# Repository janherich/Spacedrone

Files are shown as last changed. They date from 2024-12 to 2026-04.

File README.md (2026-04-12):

# Spacedrone
High-performance open-source scalable drone project
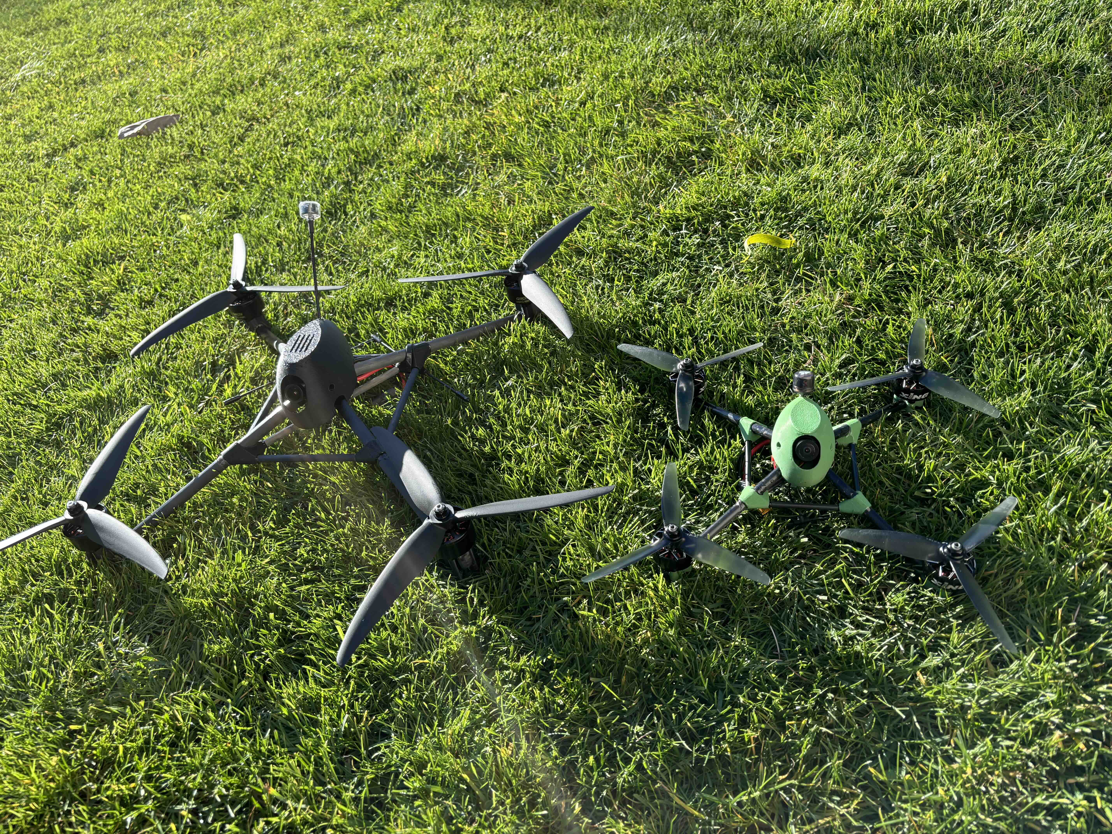
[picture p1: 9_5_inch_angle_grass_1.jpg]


<video controls width="100%" preload="metadata">
  <source src="/5_inch_pyramid_drone/video/spirited_flying.mp4" type="video/mp4">
  Your browser does not support the video tag.
</video>

# About Spacedrone
## Rationale

Spacedrone aims to approach quadrocopter design from a very different angle compared to existing projects.
It utilises efficient spaceframe structures and aerodynamic principles to create a very efficient quadcopter
design, with lowest-in-class weight and above-average frame stiffness ([7" stiffness comparison](7_inch_pyramid_drone/STIFFNESS_COMPARISON.md)) and aerodynamics.

Furthermore, it is fully parametric and scalable, covering a wide range of sizes—from small sub-250g 4–5" builds to
heavy lifters with 3115 and bigger motors.

## 5-inch racer
* [Project folder with build instructions and 3D print files](/5_inch_pyramid_drone)
* ~38g complete frame weight with aerodynamic canopy
* Recommended for milder ~1800kv 6s motors
* ~250g average build weight with powerful 2207/2306 motors, 230g possible with very light motors motors and titanium hardware
* Perfect balance with bottom mounted battery, CG in the propeller plane
* Integral cable routing in hollow 7mm round arms, no braces or additional obstructions in propeller airflow
* Aerodynamic canopy with quick attach system housing camera, vtx and RX
* Almost completely clean camera view with just small parts of motors in the bottom corners of the viewport, despite balanced true-X config
* Stiff frame capable of running aggressive PID tunes without hot-motors/vibration problems

## 5-inch HD racer
* [Project folder with build instructions and 3D print files](/5_inch_hd_pyramid_drone)
* ~48g complete frame weight with aerodynamic canopy
* Recommended for the most powerful ~2100kv 6s motors
* ~270g average build weight with powerful 2207/2306 motors, 260g possible with titanium hardware
* Perfect balance with bottom mounted battery, CG in the propeller plane
* Integral cable routing in hollow 8mm round arms, no braces or additional obstructions in propeller airflow
* Aerodynamic canopy with quick attach system housing camera, vtx and RX
* Almost completely clean camera view with just small parts of motors in the bottom corners of the viewport, despite balanced true-X config
* Stiff frame capable of running aggressive PID tunes without hot-motors/vibration problems
* Easily achieves ([240km/h+ top speed](5_inch_hd_pyramid_drone/img/flight_stats.png)) even with standard mid-pitch 5.1" tri-blades

## 7-inch long-range cruiser
* [Project folder with build instructions and 3D print files](/7_inch_pyramid_drone)
* ~60g complete frame weight with aerodynamic canopy
* ~300g average build weight with efficient 2506/2604 motors, 280g possible with smaller, lower kv 2207 or similar sized motors
* Perfect balance with bottom mounted battery, CG in the propeller plane
* Integral cable routing in hollow 8mm round arms, no braces or additional obstructions in propeller airflow
* Aerodynamic canopy with quick attach system housing camera, vtx and RX
* Very clean camera view with just small parts of propellers/motors in bottom corners of the viewport, despite balanced true-X config
* Stiff frame capable of running aggressive PID tunes without hot-motors/vibration problems ([stiffness comparison vs standard 7" frame](7_inch_pyramid_drone/STIFFNESS_COMPARISON.md))

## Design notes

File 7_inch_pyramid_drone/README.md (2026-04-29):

# Build guide

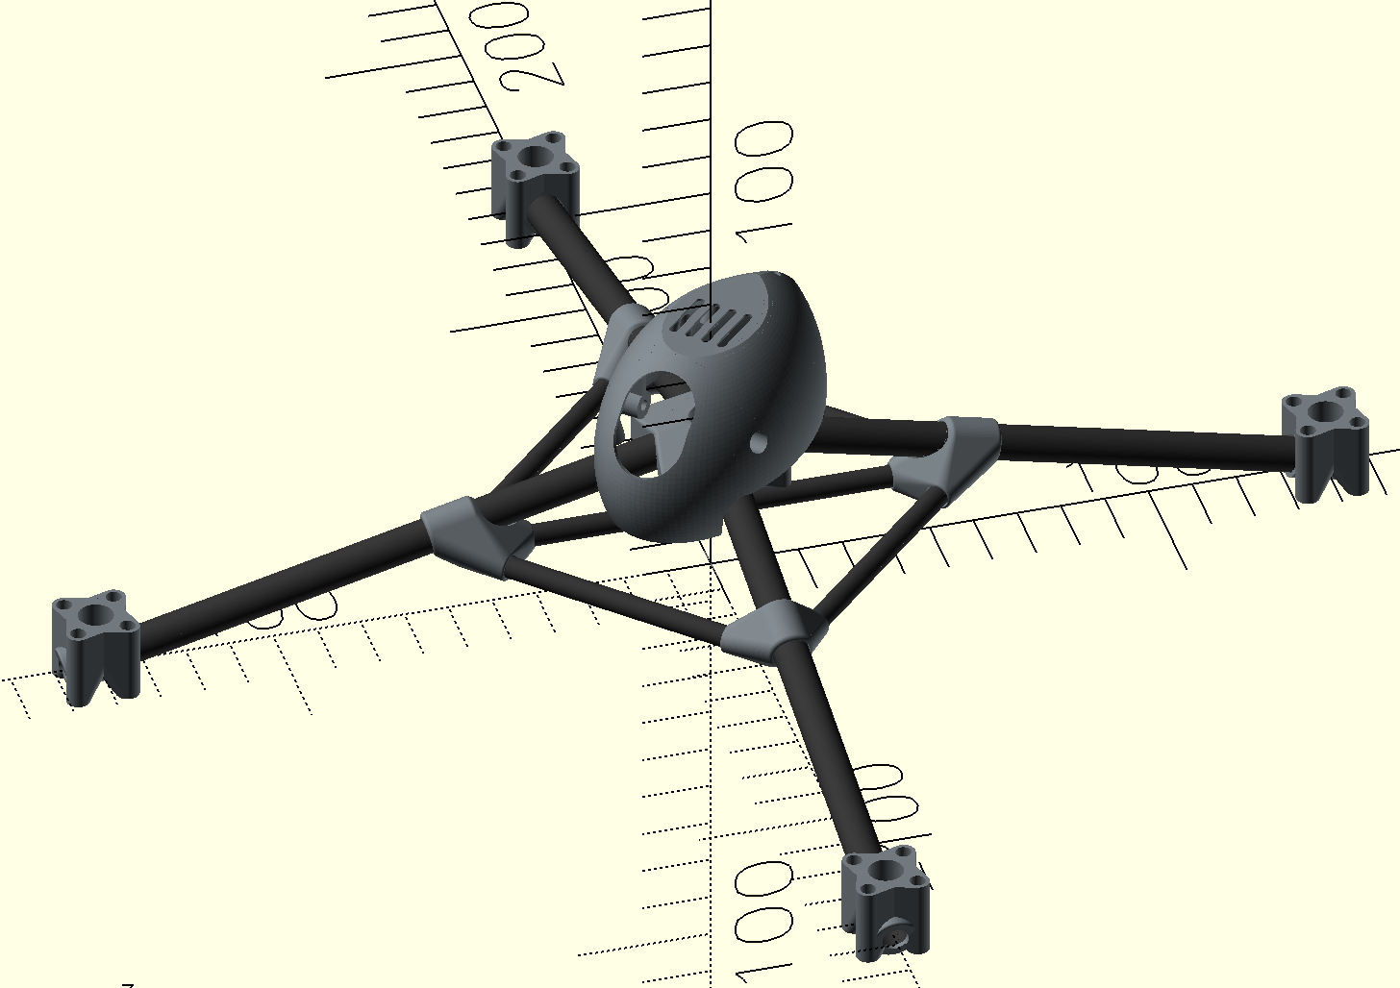
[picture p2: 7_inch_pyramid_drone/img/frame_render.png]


See [Stiffness comparison](STIFFNESS_COMPARISON.md) for test results vs a standard 7" frame.

## List of parts

### 3D Printed parts
* 1x `canopy.stl` (or `canopy_long_camera_bolts.stl`)
* 1x `central_top_node.stl`
* 2x `arm_corner_0.stl`
* 2x `arm_corner_1.stl`
* 4x `motor_mount.stl`
* 4x `canopy_snap_on_anchor.stl`
* 2x `battery_rail.stl`

### Carbon tubing
* 1x 106mm long 5x3 tube (diagonal brace)
* 4x 78.5mm long 5x3 tube (perimeter brace)
* 4x 147.6mm long 8x6 tube (arm tube)

### Metal fasteners
* 16x M3x20mm motor bolts
* 4x M2x12mm flight controller mount bolts

### Tools and consumables
* Structural epoxy, 30min set-time is ideal, or alternatively MMA adhesive
* Small cut-off saw for cutting carbon tubing (hacksaw with very fine toothed blade works as well)
* Small strip of sandpaper or flat file to scratch tube mating surfaces

### Drone parts
* 1x AIO board (Speedybee F405 AIO is a good choice)
* 4x 16mm mount pattern motors, 2506 or 2604 size is a good choice
* 4x 7-7.5" Props (7.5" is the max diameter supported by the frame)
* Small VTX with 20x20 mount pattern
* VTX Antenna with right angle MMCX connector
* Micro sized cam (19mm camera spacing)
* RX (small size; HGLRC ELRS 2.4G is a good choice)

## Assembly instructions

### Assembling the frame

Print all parts with suitable material, PETG, PC or PA12CF15 are all good choices.
PLA is brittle and its impact resistance is poor, but it's also very stiff - frame will be
the stiffest, but impact resistance will suffer.

Standard print settings with 2-3walls, 20% infill and 4 top/bottom layers are good, keep cooling
at minimum (max 40%) to achieve good layer adhesion, no supports are necessary.

Cut CFRP tubing to necessary length using cut-off saw with carbide/diamond cutting disc (fastest and cleanest method),
or manual hacksaw with fine toothed blade. 
Try to cut the tubes as precisely as possible, it's better to cut the tubes a little bit longer and carefully shorten
them to the desired length with a flat diamond file.

Once tubes are cut, you need to thoroughly scratch the mating surfaces with a flat file for a good epoxy bond.
Scratching is not necessary with raw carbon pultruded tubes, like [DPP pultruded tubes](https://www.dpp-pultrusion.com/en-NL),
it's enough to clean and degrease them with IPA.

Next step is glueing the frame together. I recommend good structural epoxy with 30min set-time - while MMA adhesives
like [MD Megabond 3000](https://www.marstondomsel.de/index.php/en/product/md-megabond-3030) provide the best strength and
impact resistance, their set-time is usually quite short and their fumes are nasty.

It's easiest to divide glueing into 3 steps:
1. First, glue motor mounts on arm tube ends—test with a dry fit before; the motor mount needs to fit on the tube without excessive force.
Mix epoxy and apply it to the scratched/sanded end of the motor arm tube, then insert the tube into motor mount.
Make sure the tube is inserted all the way and rotate it couple of times to distribute epoxy evenly.
Be careful not to clog the end of the tube with epoxy, as it needs to remain clear for motor cable routing - remove the excess epoxy with piece of paper/towel in case some got into the tube.

2. As a second step, assemble the central support perimeter with diagonal tube.
Do a dry fit test before, making sure that tubes can be inserted into corner nodes easily and perimeter is square and lying flat on workbench.
Next, mix epoxy and put it inside each support tube hole/cavity (use a wooden stick for that).
Take 2 bigger corner nodes, mount them on diagonal tube and lay it on the workbench.
Take one of the smaller corner pieces and put 2 perimeter tubes into holes/sockets, repeat the same process for the last corner piece.
In the final assembly step, pull the 2 bigger corners with the diagonal tube a little bit apart and join them with the rest of the pieces.
Once every tube is inside corner piece socket, press all corners together with your fingers and lay it flat on workbench.
You will need to wait till the epoxy cures for the last step.

3. Next, prepare the arm tubes with already mounted motor mounts (step 1) - make sure the through holes for 12mm long motor bolts are clear and bolts
can be inserted without problems. 
Once all bolt channels are ready, mount the bolts into motor mount, fixing them with nuts on the other side, so they don't fall out.
Alternatively, you can already mount motors, making sure the motor wires are facing outside the frame center, exactly opposite how would you normally mount them on a classic quad frame.

Test fit by inserting arm tubes (already with attached motor mounts) through the corners and joining them together with the central top node.
The best way to do it is to first put 2 arm tubes through the smaller corner nodes (the ones joined by just 2 perimeter tubes, without the diagonal tube), and join them with the central node.
You can then use the cable hole in the central node + diagonal tube below it to visually center the arm tubes - put the remaining 2 arm tubes through the bigger perimeter corners afterwards and join them in the central node as well.
They should fit easily without excessive force and you should be able to easily rotate the arm tubes when the whole frame is assembled.
Put the frame on flat workbench, arm ends with motor mounts should be level when they rest on motor bolt heads and frame shouldn't be twisted, all 4 arm ends should be touching the bench.

Next, pull the arm tubes a little bit (1–2 cm) apart and remove the central node.
Mix epoxy and spread it on the arm tube just outside of the perimeter corner, cover a ~10mm band on the tube with epoxy, don't put too much there, just a thin layer.
Lift the frame (hold it by the perimeter tubes; avoid touching epoxied or to-be-epoxied parts) and slowly push the arm tube you just epoxied ~2 cm inside through the corner piece while rotating it at the same time, then pull it back.
The aim is to evenly spread the epoxy inside the corner piece, repeat for each arm-tube/corner.
As a last step, spread epoxy on arm-tube ends (to be joined by the central top node), be careful to just spread it on the outside of the tube. Attach the central node, using the same sequence of steps as described
above in the (dry) fit test section, rotate each arm tube 2-3 times to spread the epoxy evenly, make sure that each tube is inserted fully to the end-stop in the central node and put the frame on flat workbench.
Make sure everything is aligned and level and wait for the epoxy to fully cure.

### Assembling the canopy housing

Put a bit of glue (epoxy or CA) on protruding sticks of canopy anchors and insert them into canopy anchor sockets.
Rotate the anchors in correct fashion - you can snap the canopy on frame and the anchors will align, wait for glue to set before removing the canopy.

### Mounting frame components

1, Start by mounting motors, bolt each motor to mount on arm end in such a way that wires face outside of the frame center. 
Do not shorten the motor wires, you need at least 20cm long wires when routed internally.
Guide the wires through the hollow arm tube till you can see the wire ends in central node hole, then "fish" them out from the top hole with tweezers or a small piece of bent wire. 
Once you have all 3 motor wires out tie them together with a small strip of tape, so you don't mix up wires from separate motors later, 
when soldering them to ESC pads. 
You can even color mark wire before routing them through the tube, so you can solder them in the right order and you don't have to mess with motor direction in firmware later.

An alternative and slightly easier way is to mount motors in a standard way, with wires facing inwards, simply taped to the tube top side.
I think it's a shame to not take advantage of the unique internal routing capability of this frame and resulting better aesthetics & aerodynamics, but it's up to you.

2. Prepare AIO board by soldering battery leads, capacitor and CAM/VTX/RX connections.

3. Mount AIO board by placing it between top node and diagonal bracing tube and screwing bolts (M2x12mm) directly to holes in the central node.
Board needs to be flipped upside down, so that USB connector and solder pads are accessible.

After board is fixed, solder the motor wires to ESC pads.

4. Fix the camera inside canopy with side bolts, connect it to camera wire from AIO.
Guide the antenna with MMCX connector through the antenna tube and connect it to VTX.
Mount the VTX with 2 M2 bolts into the VTX screw-in sockets; fix the RX board with double-sided tape inside the canopy,
good place is front below the camera window for front mounted rx antenna/s, or rear of the canopy for rear rx antenna location.
Now you can tuck-in all connector wires inside canopy and snap canopy in place.

5. Secure RX antenna with zip tie or electrical tape on front or rear arm (8mm).
Secure battery leads from AIO on rear perimeter tube (5mm) with zip tie as well.

### Mounting battery

Battery is mounted below the frame between 2 snap-on battery rails.
Adjust their width to fit the chosen battery; you can also tape non-slip silicone strips on the rails for better grip.
Battery securing strip is threaded just below the diagonal tube.

For Betaflight setup and flight video, see **[Configuration](CONFIGURATION.md)**.

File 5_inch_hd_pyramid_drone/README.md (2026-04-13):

# Build guide

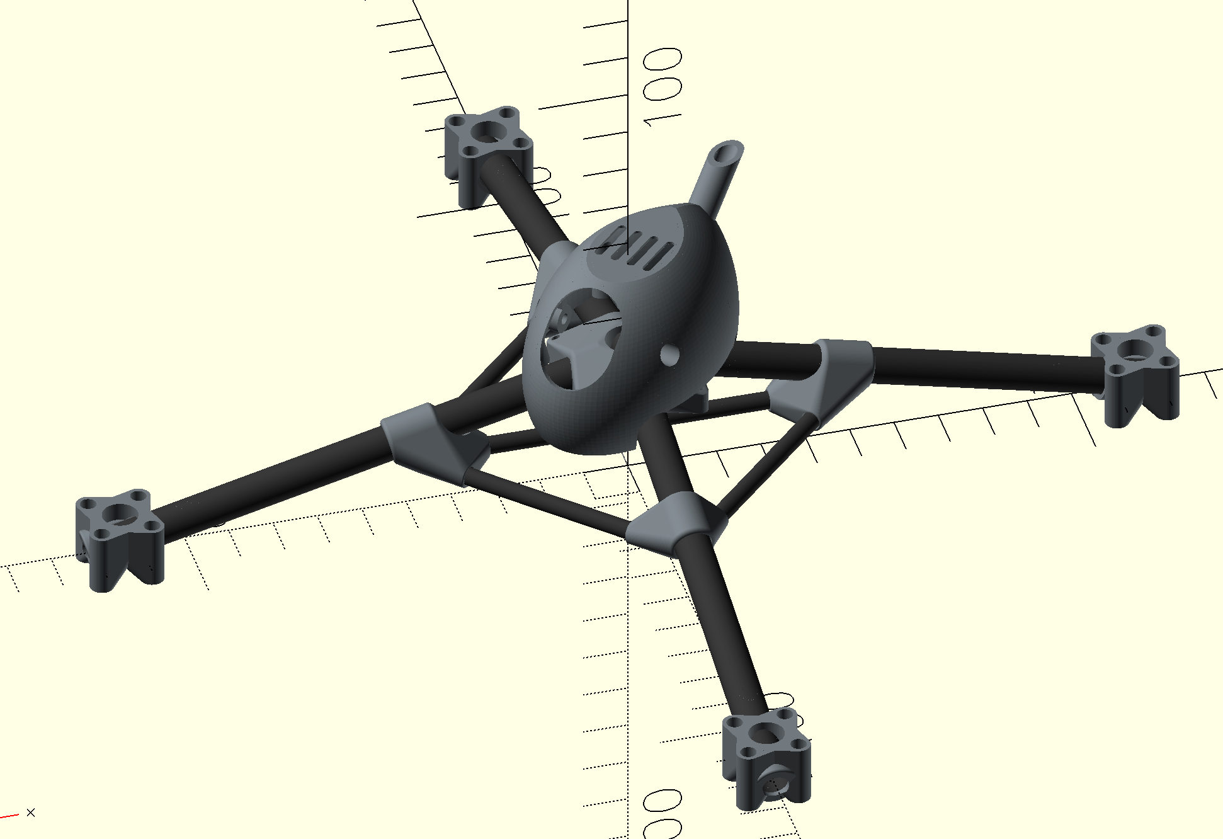
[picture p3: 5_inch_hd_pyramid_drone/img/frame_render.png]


## List of parts

### 3D Printed parts
* 1x `canopy.stl` (or `canopy_long_camera_bolts.stl`)
* 1x `central_top_node.stl`
* 2x `arm_corner_0.stl`
* 2x `arm_corner_1.stl`
* 4x `motor_mount.stl`
* 4x `canopy_snap_on_anchor.stl`
* 2x `battery_rail.stl`
* (Optional) 1x `gps_mount.stl`

### Carbon tubing
* 1x 87.1mm long 4x2 tube (diagonal brace)
* 4x 64.5mm long 4x2 tube (perimeter brace)
* 4x 120.5mm long 8x6 tube (arm tube)

### Metal fasteners
* 16x M3x16mm motor bolts
* 4x M2x12mm flight controller mount bolts

### Tools and consumables
* Structural epoxy, 30min set-time is ideal, or alternatively MMA adhesive
* Small cut-off saw for cutting carbon tubing (hacksaw with very fine toothed blade works as well)
* Small strip of sandpaper or flat file to scratch tube mating surfaces

### Drone parts
* 1x AIO board (Speedybee F405 AIO is a good choice)
* 4x 16mm mount pattern motors, 2207 size is a good choice
* 4x 5-6" Props (6" is the max diameter supported by the frame)
* Small size race type VTX (DarwinFPV Ape 25-600mW is a good choice)
* Short (40mm) u.FL antenna
* Micro sized cam (19mm camera spacing)
* RX (small size; HGLRC ELRS 2.4G is a good choice)
* (Optional) small GPS chip (HGLRC M100 Mini GPS)

## Assembly instructions

### Assembling the frame

Print all parts with suitable material, PETG, PC or PA12CF15 are all good choices.
PLA is brittle and its impact resistance is poor, but it's also very stiff - frame will be
the stiffest, but impact resistance will suffer.

Standard print settings with 2-3walls, 20% infill and 4 top/bottom layers are good, keep cooling
at minimum (max 40%) to achieve good layer adhesion, no supports are necessary.

Cut CFRP tubing to necessary length using cut-off saw with carbide/diamond cutting disc (fastest and cleanest method),
or manual hacksaw with fine toothed blade. 
Try to cut the tubes as precisely as possible, it's better to cut the tubes a little bit longer and carefully shorten
them to the desired length with a flat diamond file.

Once tubes are cut, you need to thoroughly scratch the mating surfaces with a flat file for a good epoxy bond.
Scratching is not necessary with raw carbon pultruded tubes, like [DPP pultruded tubes](https://www.dpp-pultrusion.com/en-NL),
it's enough to clean and degrease them with IPA.

Next step is glueing the frame together. I recommend good structural epoxy with 30min set-time - while MMA adhesives
like [MD Megabond 3000](https://www.marstondomsel.de/index.php/en/product/md-megabond-3030) provide the best strength and
impact resistance, their set-time is usually quite short and their fumes are nasty.

It's easiest to divide glueing into 3 steps:
1. First, glue motor mounts on arm tube ends—test with a dry fit before; the motor mount needs to fit on the tube without excessive force.
Mix epoxy and apply it to the scratched/sanded end of the motor arm tube, then insert the tube into motor mount.
Make sure the tube is inserted all the way and rotate it couple of times to distribute epoxy evenly.
Be careful not to clog the end of the tube with epoxy, as it needs to remain clear for motor cable routing - remove the excess epoxy with piece of paper/towel in case some got into the tube.

2. As a second step, assemble the central support perimeter with diagonal tube.
Do a dry fit test before, making sure that tubes can be inserted into corner nodes easily and perimeter is square and lying flat on workbench.
Next, mix epoxy and put it inside each support tube hole/cavity (use a wooden stick for that).
Take 2 bigger corner nodes, mount them on diagonal tube and lay it on the workbench.
Take one of the smaller corner pieces and put 2 perimeter tubes into holes/sockets, repeat the same process for the last corner piece.
In the final assembly step, pull the 2 bigger corners with the diagonal tube a little bit apart and join them with the rest of the pieces.
Once every tube is inside corner piece socket, press all corners together with your fingers and lay it flat on workbench.
You will need to wait till the epoxy cures for the last step.

3. Next, prepare the arm tubes with already mounted motor mounts (step 1) - make sure the through holes for 12mm long motor bolts are clear and bolts
can be inserted without problems. 
Once all bolt channels are ready, mount the bolts into motor mount, fixing them with nuts on the other side, so they don't fall out.
Alternatively, you can already mount motors, making sure the motor wires are facing outside the frame center, exactly opposite how would you normally mount them on a classic quad frame.

Test fit by inserting arm tubes (already with attached motor mounts) through the corners and joining them together with the central top node.
The best way to do it is to first put 2 arm tubes through the smaller corner nodes (the ones joined by just 2 perimeter tubes, without the diagonal tube), and join them with the central node.
You can then use the cable hole in the central node + diagonal tube below it to visually center the arm tubes - put the remaining 2 arm tubes through the bigger perimeter corners afterwards and join them in the central node as well.
They should fit easily without excessive force and you should be able to easily rotate the arm tubes when the whole frame is assembled.
Put the frame on flat workbench, arm ends with motor mounts should be level when they rest on motor bolt heads and frame shouldn't be twisted, all 4 arm ends should be touching the bench.

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

### Assembling the canopy housing

Put a bit of glue (epoxy or CA) on protruding sticks of canopy anchors and insert them into canopy anchor sockets.
Rotate the anchors in correct fashion - you can snap the canopy on frame and the anchors will align, wait for glue to set before removing the canopy.

### Mounting frame components

1, Start by mounting motors, bolt each motor to mount on arm end in such a way that wires face outside of the frame center. 
Do not shorten the motor wires, you need at least 15cm long wires when routed internally.
Guide the wires through the hollow arm tube till you can see the wire ends in central node hole, then "fish" them out from the top hole with tweezers or a small piece of bent wire. 
Once you have all 3 motor wires out tie them together with a small strip of tape, so you don't mix up wires from separate motors later, 
when soldering them to ESC pads. 
You can even color mark wire before routing them through the tube, so you can solder them in the right order and you don't have to mess with motor direction in firmware later.

An alternative and slightly easier way is to mount motors in a standard way, with wires facing inwards, simply taped to the tube top side.
I think it's a shame to not take advantage of the unique internal routing capability of this frame and resulting better aesthetics & aerodynamics, but it's up to you.

2. Prepare AIO board by soldering battery leads, capacitor and CAM/VTX/RX connections.

3. Mount AIO board by placing it between top node and diagonal bracing tube and screwing bolts (M2x12mm) directly to holes in the central node.
Board needs to be flipped upside down, so that USB connector and solder pads are accessible.

After board is fixed, solder the motor wires to ESC pads.

4. Fix the camera inside canopy with side bolts, connect it to camera wire from AIO.
Guide the short VTX antenna with uFL connector through the antenna tube and connect it to VTX.
Fix VTX with a piece of double-sided tape on the canopy roof; fix the RX board with double-sided tape inside the canopy as well,
good place is front below the camera window.
Now you can tuck-in all connector wires inside canopy and snap canopy in place.

5. Secure RX antenna with zip tie or electrical tape on one of the front arms (7mm) or front perimeter tube (4mm) if you use antenna with short lead.
Secure battery leads from AIO on rear perimeter tube (4mm) with zip tie as well.

### Mounting battery

Battery is mounted below the frame between 2 snap-on battery rails.
Adjust their width to fit the chosen battery; you can also tape non-slip silicone strips on the rails for better grip.
Battery securing strip is threaded just below the diagonal tube.

For Betaflight setup and flight video, see **[Configuration](CONFIGURATION.md)**.

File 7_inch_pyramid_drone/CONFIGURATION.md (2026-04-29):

# Configuration

Betaflight tuning for this build. For assembly, see the [build instructions](README.md).

## Betaflight

Make sure to correctly adjust board/gyro position as flipped because you mounted the board upside down, make sure to verify it's behaving correctly.
Also make sure to correctly assign motors and their direction in the motors tab, especially when you didn't mark the motor wires when routing them internally through arm tubes.

The quad flies very well on standard betaflight settings, even better with RPM filtering enabled and 7" Supafly preset.
Due to the very low weight and low disc loading, set RPM for dynamic idle quite low (~12); otherwise low-throttle management is quite difficult and the quad feels very floaty.
As you can see in the video, it's a super stable platform, perfect for precise hovering on spot.

## Flight video

<video controls width="100%" preload="metadata">
  <source src="video/flight_video.mp4" type="video/mp4">
  Your browser does not support the video tag.
</video>

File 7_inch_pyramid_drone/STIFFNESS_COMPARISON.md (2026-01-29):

# Stiffness comparison: Spacedrone vs standard 7" frame

This document summarizes a simple stiffness comparison between a conventional 7" quad frame and the 7" Spacedrone frame. The goal was to quantify how the spaceframe design and carbon tubing perform under bending and torsion compared to a typical plate-based frame.

## Test frames

| Frame | Complete frame weight | Construction |
|---|---|---|
| **Stock** | 141 g | Conventional plate-based 7" frame |
| **Spacedrone** | 65 g | Carbon tubing spaceframe with 3D-printed nodes |

The Spacedrone frame is roughly **half the weight** of the stock frame while targeting similar or better stiffness in key directions.

---

## Bending stiffness (top load)

A **3 kg** weight was applied vertically at the top centre of the frame (above the flight controller area). Displacement was measured at the load point.

### Results

| Frame | Displacement | Relative stiffness |
|---|---|---|
| Stock | 0.97 mm | 1× (baseline) |
| Spacedrone | 0.14 mm | **~7× stiffer** |

The Spacedrone frame showed **about 7× higher bending stiffness** under this load, with 0.14 mm deflection vs 0.97 mm for the stock frame.

### Test setup (Spacedrone)

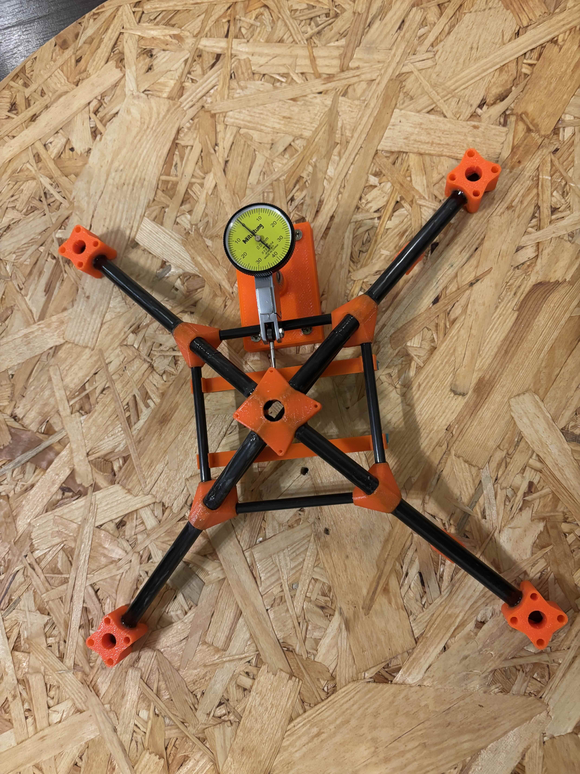
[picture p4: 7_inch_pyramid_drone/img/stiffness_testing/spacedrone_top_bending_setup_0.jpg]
Spacedrone bending test setup


*Bending test setup: 3 kg weight applied at the top centre.*

### Loaded (comparison)

**Spacedrone under 3 kg load (0.14 mm displacement):**

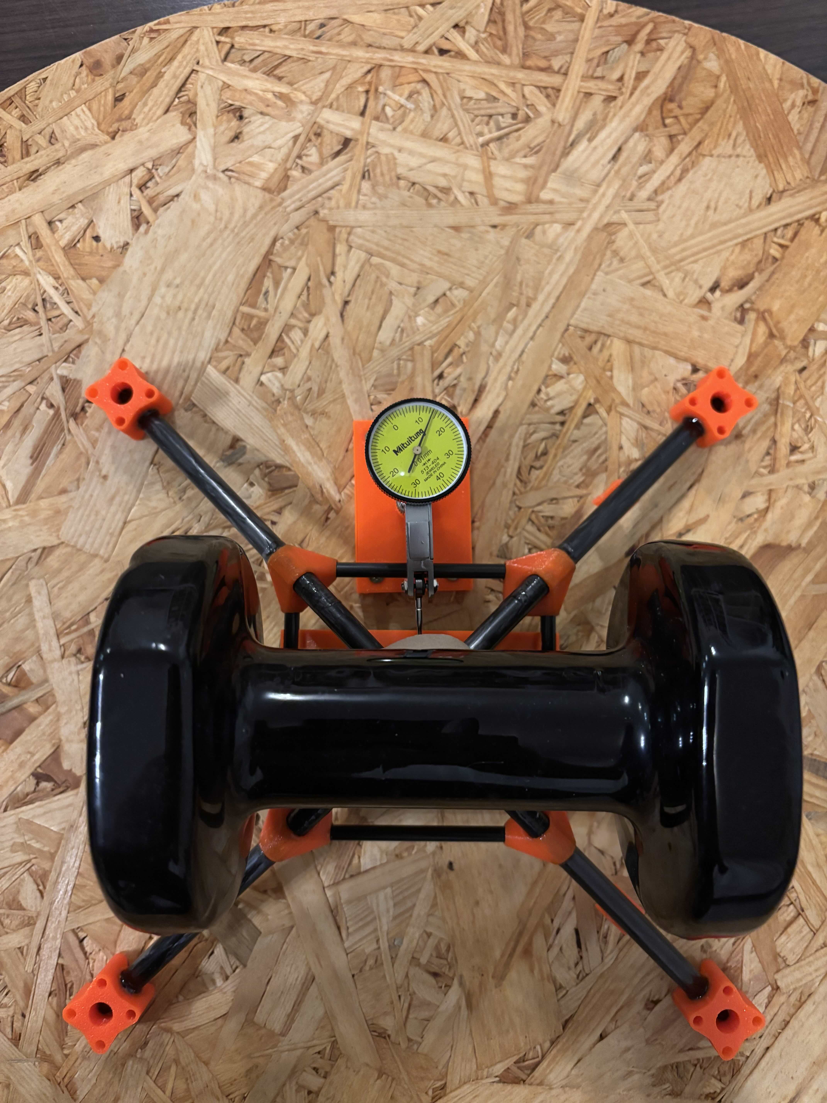
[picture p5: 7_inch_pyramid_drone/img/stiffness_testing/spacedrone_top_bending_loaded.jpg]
Spacedrone bending loaded


**Stock frame under same 3 kg load (0.97 mm displacement):**

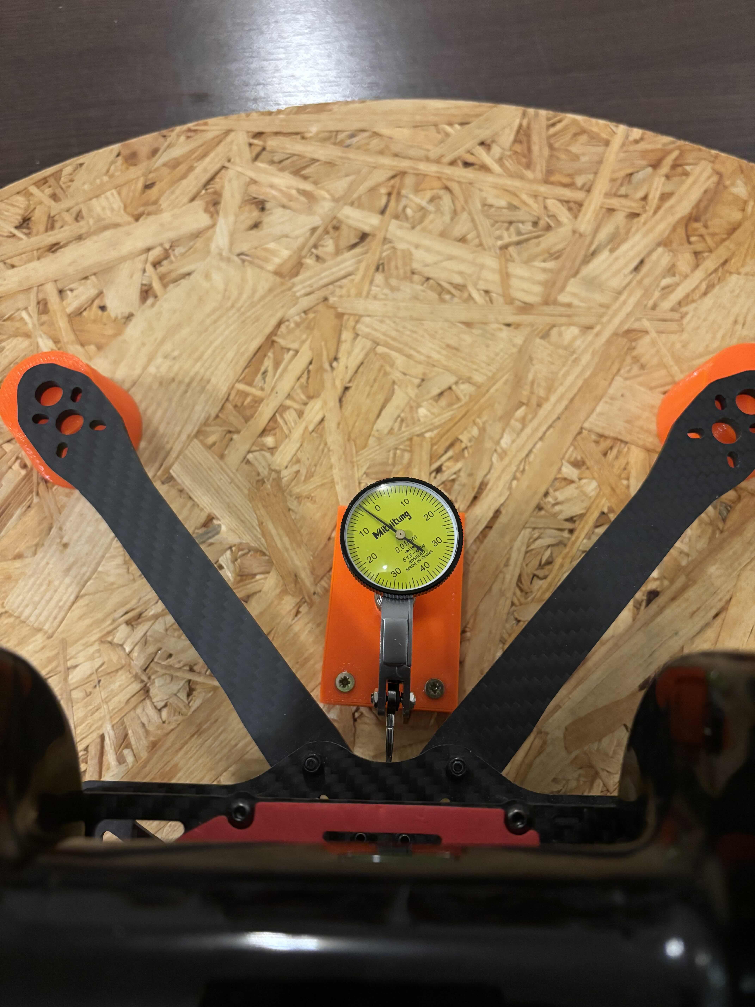
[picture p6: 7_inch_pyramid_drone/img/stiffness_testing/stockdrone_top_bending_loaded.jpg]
Stock frame bending loaded


---

## Torsional stiffness

A **200 g** weight was placed **27 cm** from the centre of rotation to apply a torsional moment. Displacement was measured at the point of load.

### Results

| Frame | Displacement | Relative stiffness |
|---|---|---|
| Stock | 1.04 mm | 1× (baseline) |
| Spacedrone | 0.73 mm | **~1.4× stiffer**  |

The Spacedrone frame was **more than 1.4× stiffer in torsion**, with 0.73 mm vs 1.04 mm displacement.

### Test setup (Spacedrone)

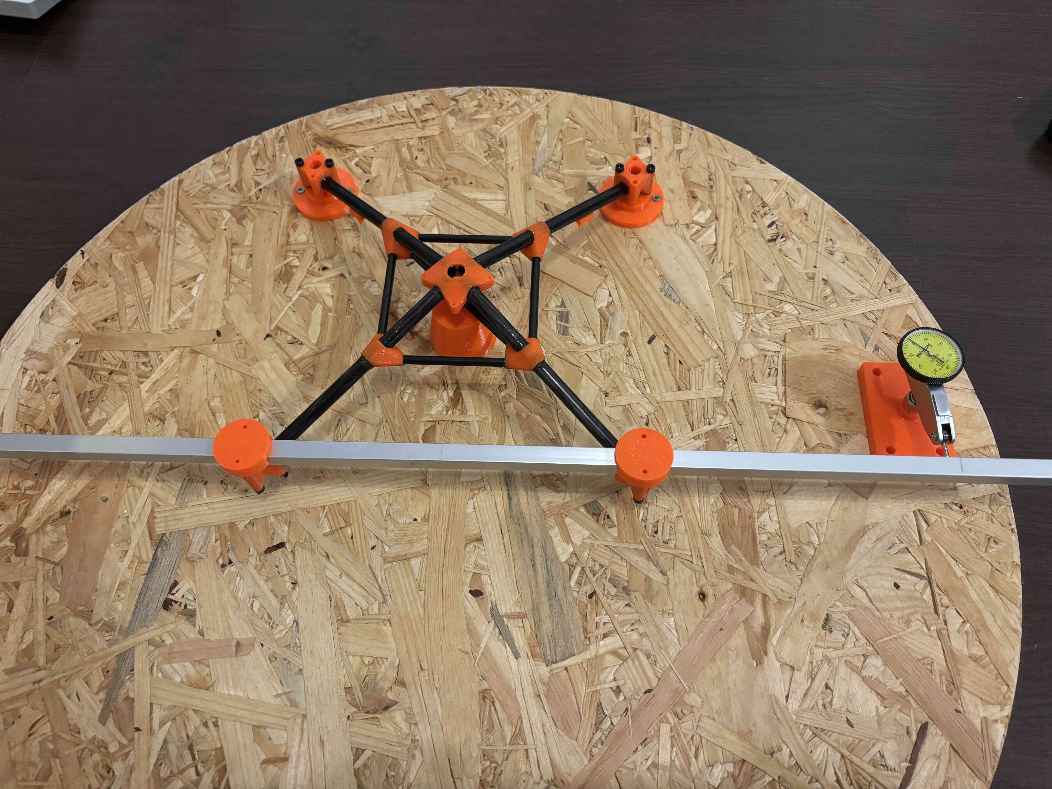
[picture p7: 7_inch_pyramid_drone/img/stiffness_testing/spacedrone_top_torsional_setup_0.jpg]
Spacedrone torsional test setup


*Torsional test setup: 200 g weight at 27 cm from centre.*

### Torsional load (200 g @ 27 cm)

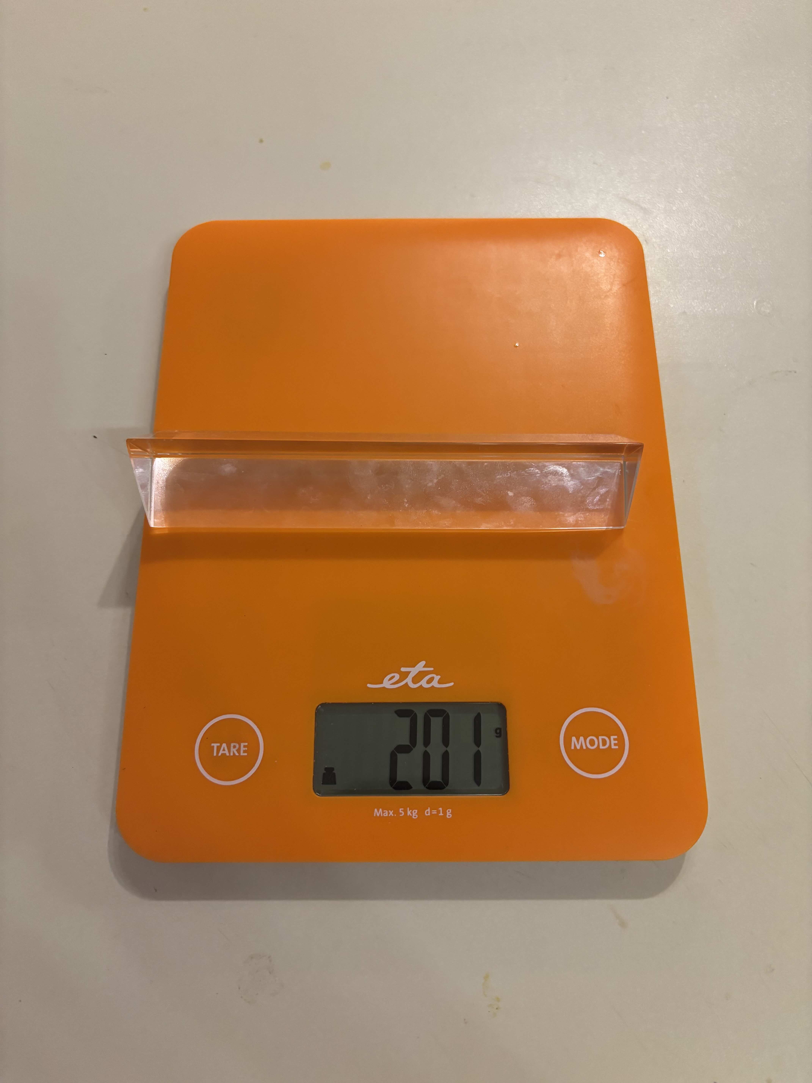
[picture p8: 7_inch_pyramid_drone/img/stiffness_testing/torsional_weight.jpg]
Torsional weight


*Weight used for torsional moment.*

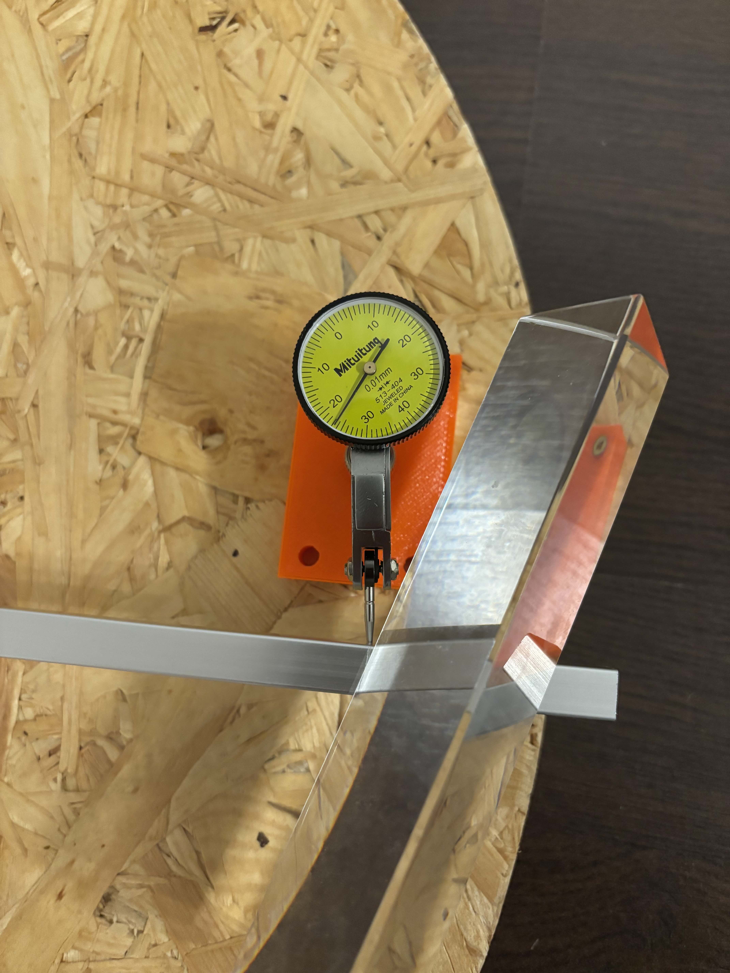
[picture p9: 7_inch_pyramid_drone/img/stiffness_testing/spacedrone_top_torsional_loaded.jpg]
Spacedrone torsional loaded


*Spacedrone under torsional load (0.73 mm displacement).*

---

## Summary

| Test | Stock (141 g) | Spacedrone (65 g) | Spacedrone advantage |
|---|---|---|---|
| **Bending** (3 kg top) | 0.97 mm | 0.14 mm | **~7× stiffer** |
| **Torsion** (200 g @ 27 cm) | 1.04 mm | 0.73 mm | **~1.4× stiffer** |

At roughly **54% less frame weight**, the 7" Spacedrone achieves:

- **~7×** higher bending stiffness (top load).
- **~1.4×** higher torsional stiffness.

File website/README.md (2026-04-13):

# Spacedrone website (Eleventy)

Informational site built from the repo’s markdown. Single source of truth: edit the docs in the repo; the site is generated from them.

## Local development

```bash
# From repo root
npm install
npm run serve
```

Then open http://localhost:8080 (or the URL Eleventy prints).

## Build

```bash
npm run build
```

Output is in `_site/`.

## GitHub Pages

1. In the repo: **Settings → Pages → Build and deployment → Source: GitHub Actions**.
2. Push to `main` (or run the workflow manually). The workflow builds Eleventy and deploys `_site` to GitHub Pages.
3. Site URL: `https://<username>.github.io/Spacedrone/` (or your custom domain if configured).

## Custom domain

In **Settings → Pages**, set your custom domain. GitHub will show DNS instructions. The site works with or without `pathPrefix`; the workflow sets it for project-pages URLs.

## Structure

- **Content**: Pulled from `README.md`, each drone’s `README.md`, `CONFIGURATION.md`, and `7_inch_pyramid_drone/STIFFNESS_COMPARISON.md` via the `contentFromMarkdown` shortcode. Do not duplicate that content in the website folder.
- **Layout & data**: `_includes/base.njk`, `_data/site.json` (nav, title, repo link).
- **Pages**: `index.njk`, and per-drone folders (`5-inch/`, `5-inch-hd/`, `7-inch/`) with `index.njk` (sample build), `build-guide.njk` (README), and for 7-inch `stiffness.njk` — each sets front matter for markdown, image base, and `buildKey` where needed.
- **Styling**: `assets/css/style.css` (edit freely).

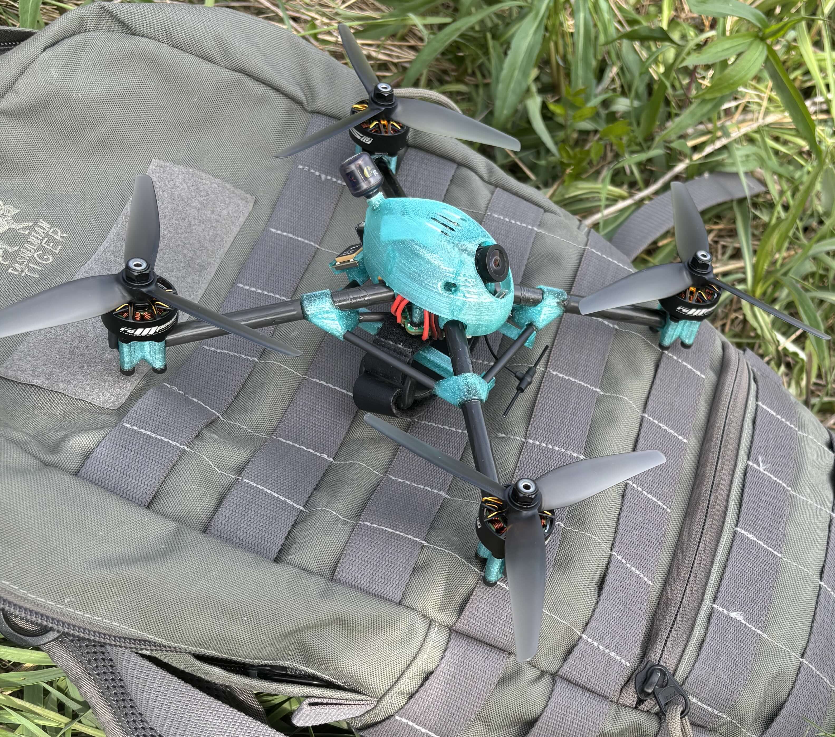
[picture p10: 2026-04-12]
5_inch_hd_pyramid_drone/img/preflight_7.jpg

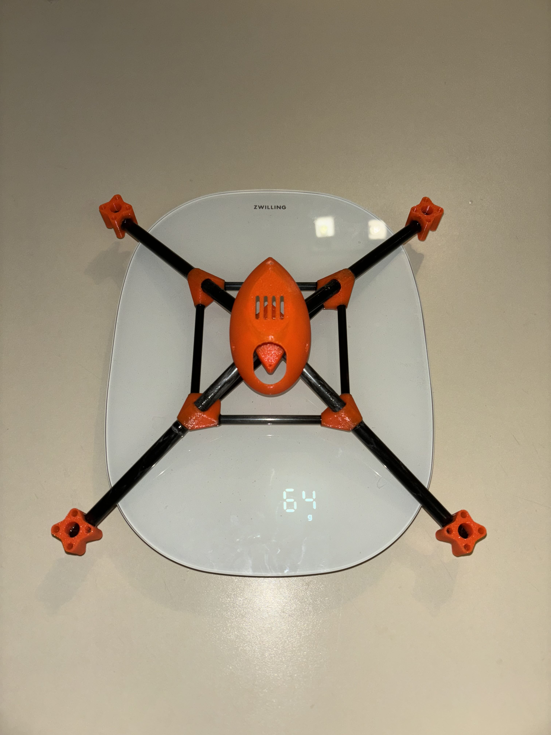
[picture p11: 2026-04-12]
7_inch_pyramid_drone/img/7_inch_frame_weight.jpg

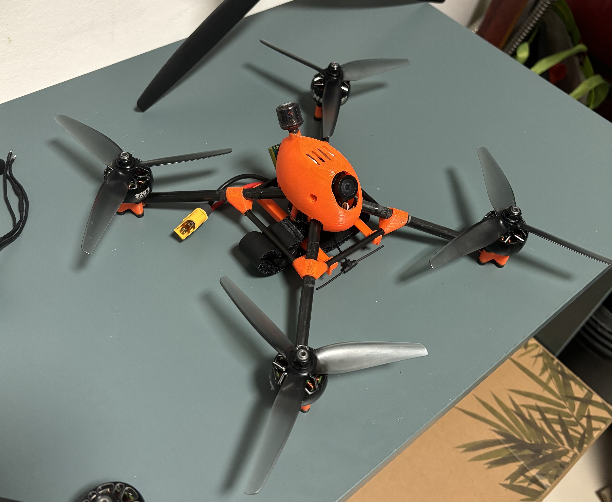
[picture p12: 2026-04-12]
5_inch_pyramid_drone/img/5_inch_aero_6s_petg_0.jpeg

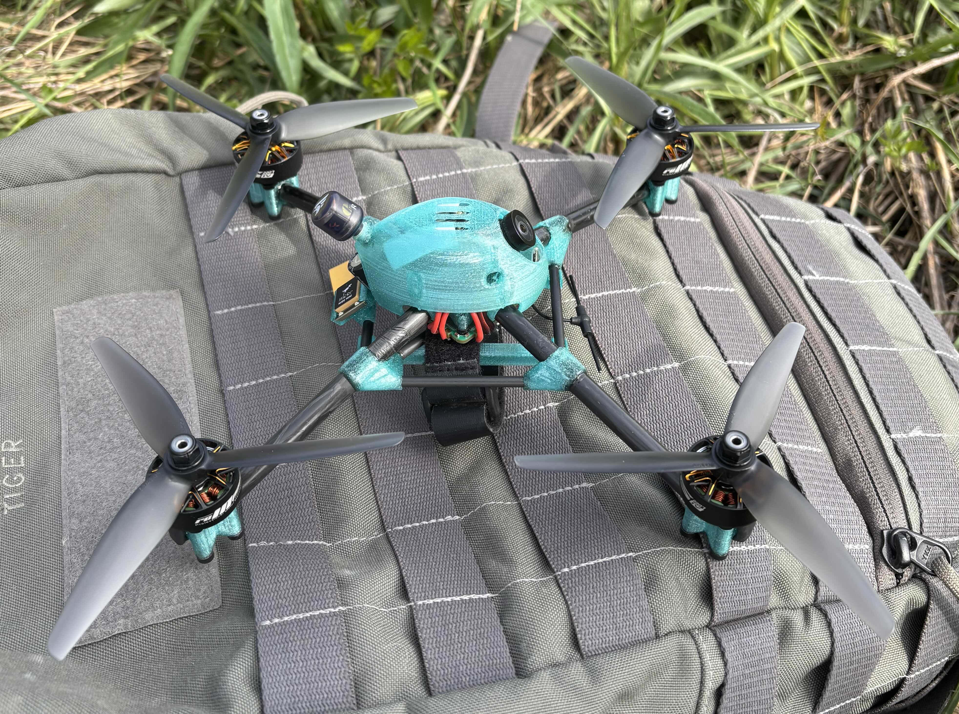
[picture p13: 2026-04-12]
5_inch_hd_pyramid_drone/img/preflight_6.jpg

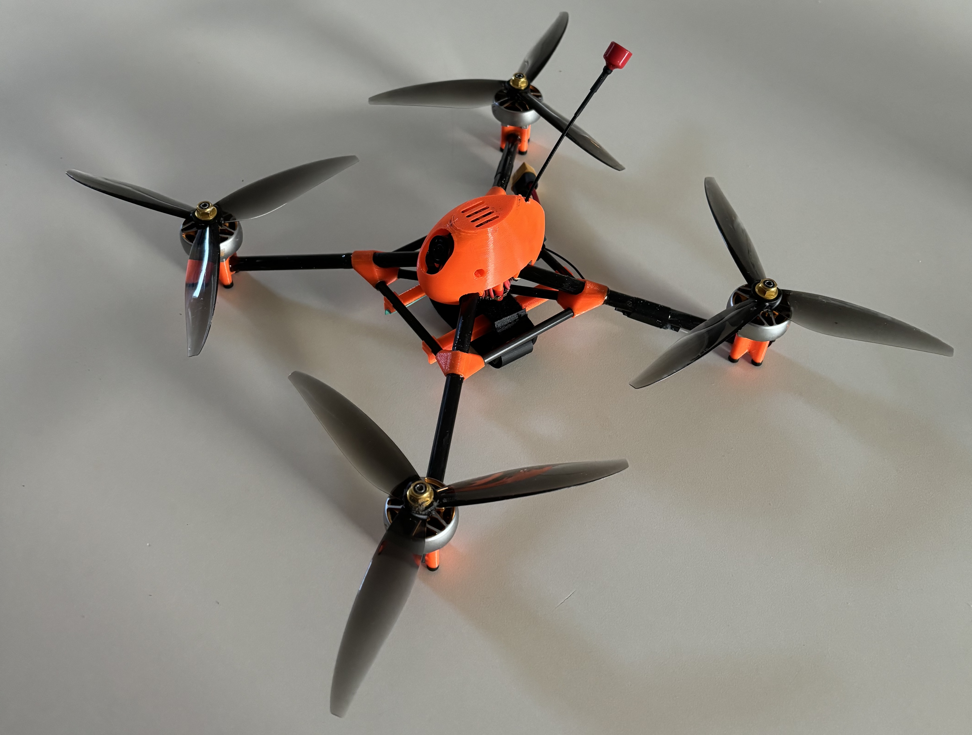
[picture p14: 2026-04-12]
7_inch_pyramid_drone/img/7_inch_4s_aero_petg_2.jpg

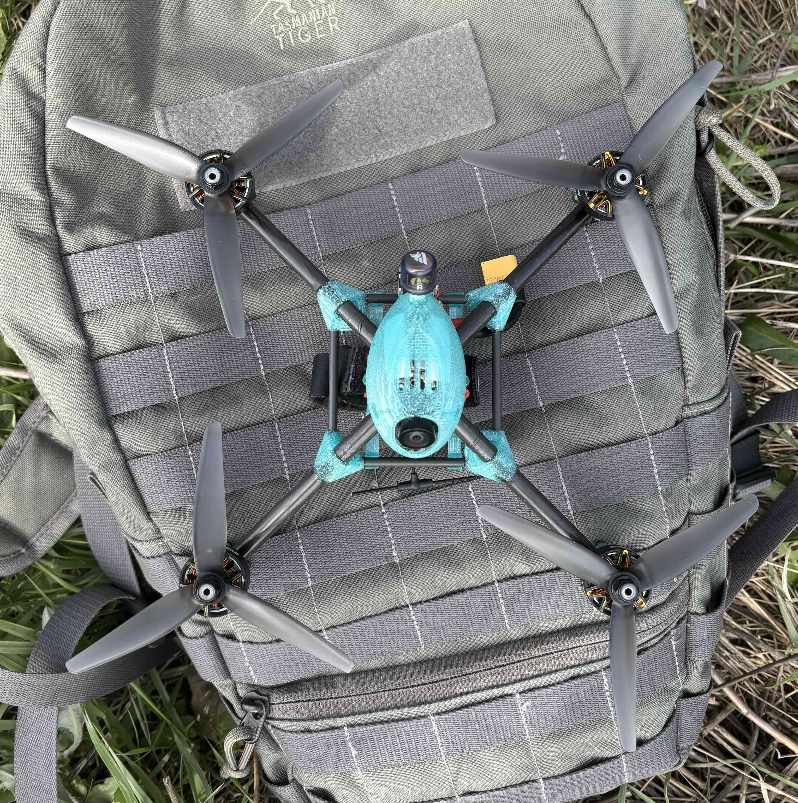
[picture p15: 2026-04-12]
5_inch_hd_pyramid_drone/img/preflight_5.jpg

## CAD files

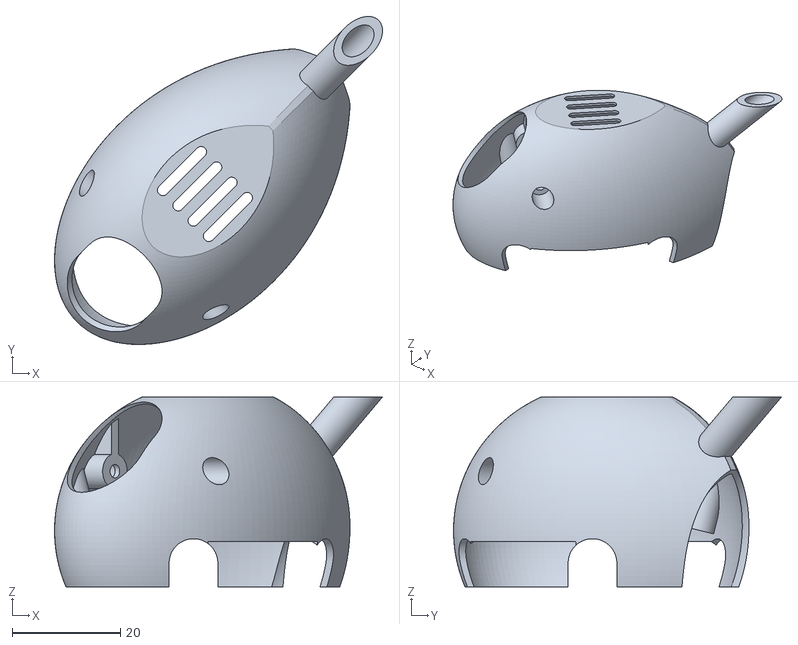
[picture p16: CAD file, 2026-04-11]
5_inch_hd_pyramid_drone/3D_prints/canopy.stl
60.6 x 60.6 x 35.1

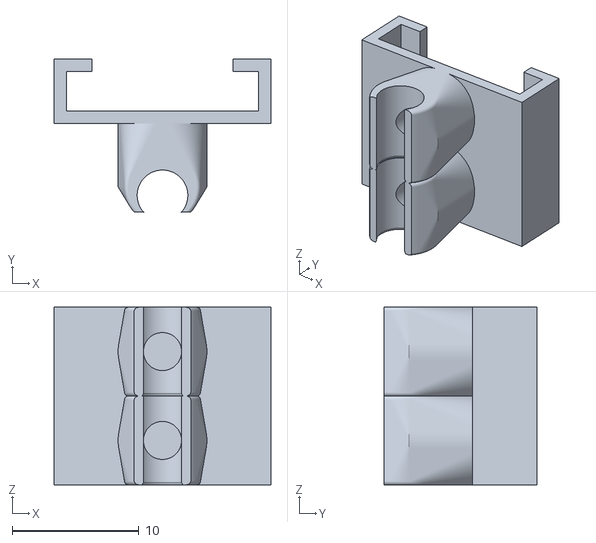
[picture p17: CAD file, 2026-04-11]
5_inch_pyramid_drone/3D_prints/gps_mount.stl
17.1 x 12.1 x 14.0

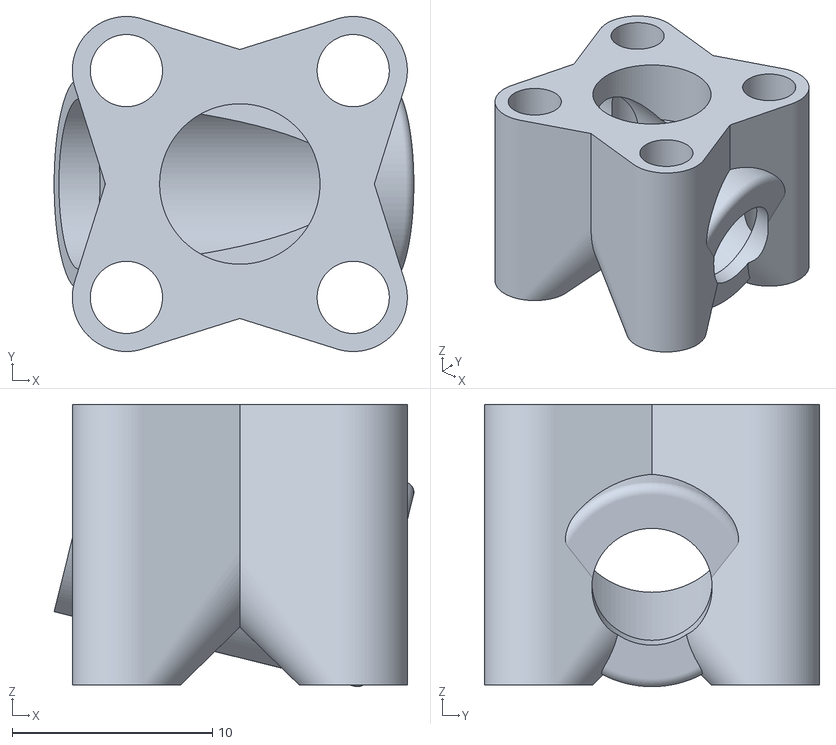
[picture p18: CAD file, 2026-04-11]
5_inch_hd_pyramid_drone/3D_prints/motor_mount.stl
17.9 x 16.7 x 14.1

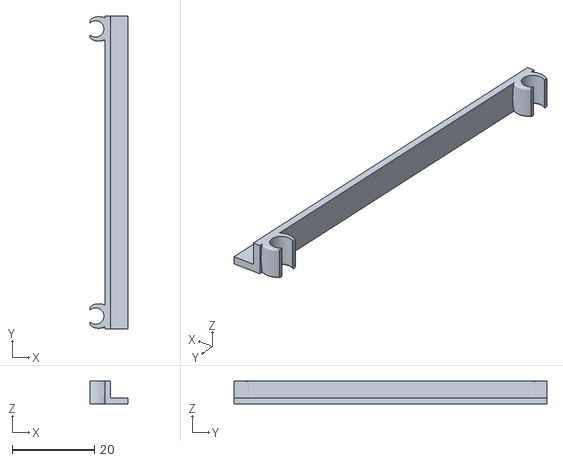
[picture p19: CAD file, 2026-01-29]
5_inch_pyramid_drone/3D_prints/battery_rail.stl
9.14 x 76.3 x 5.60

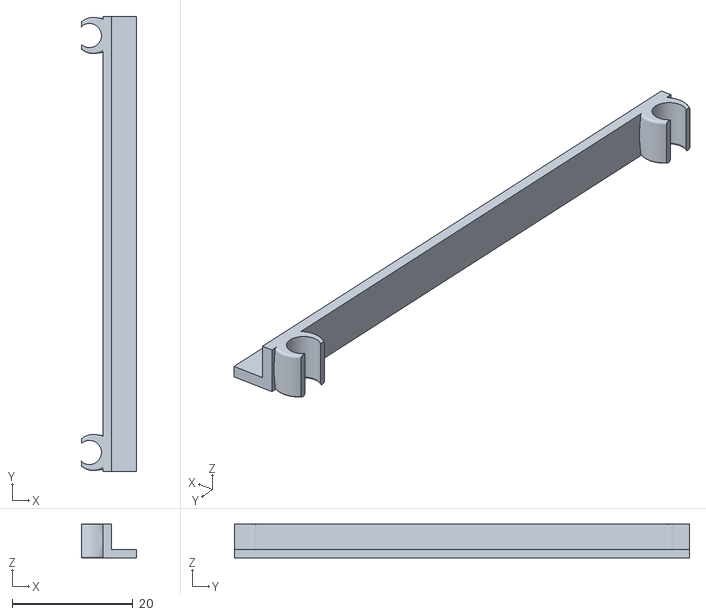
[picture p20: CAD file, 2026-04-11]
5_inch_hd_pyramid_drone/3D_prints/battery_rail.stl
9.14 x 75.3 x 5.60

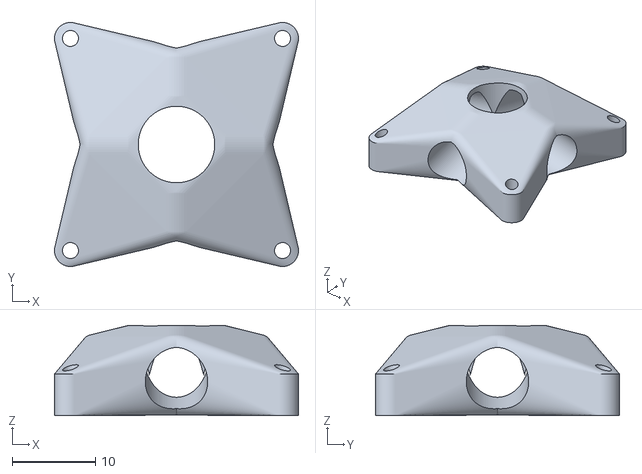
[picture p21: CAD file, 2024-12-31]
5_inch_pyramid_drone/3D_prints/central_top_node.stl
29.3 x 29.3 x 10.8

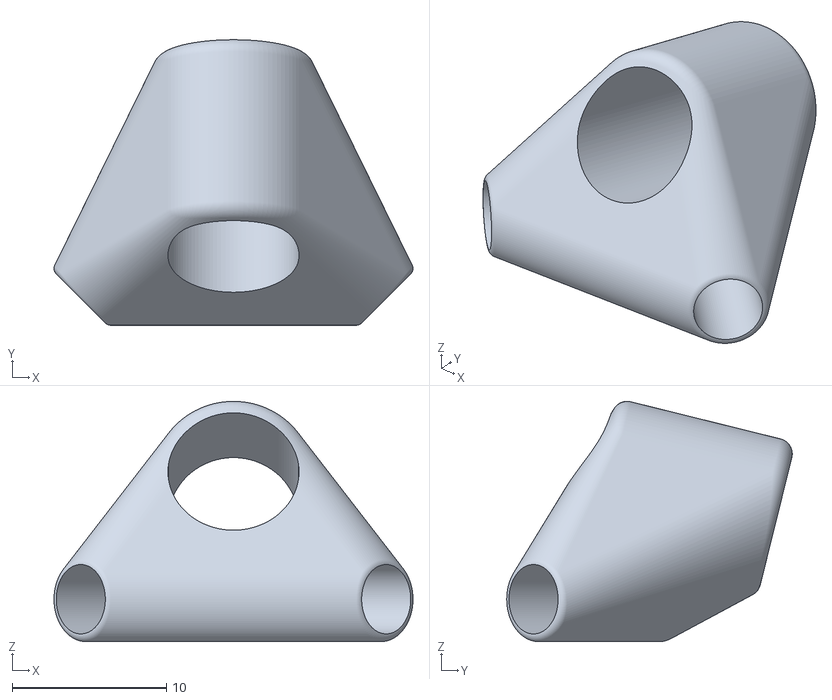
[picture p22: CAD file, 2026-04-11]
5_inch_hd_pyramid_drone/3D_prints/arm_corner_1.stl
23.3 x 18.5 x 15.6

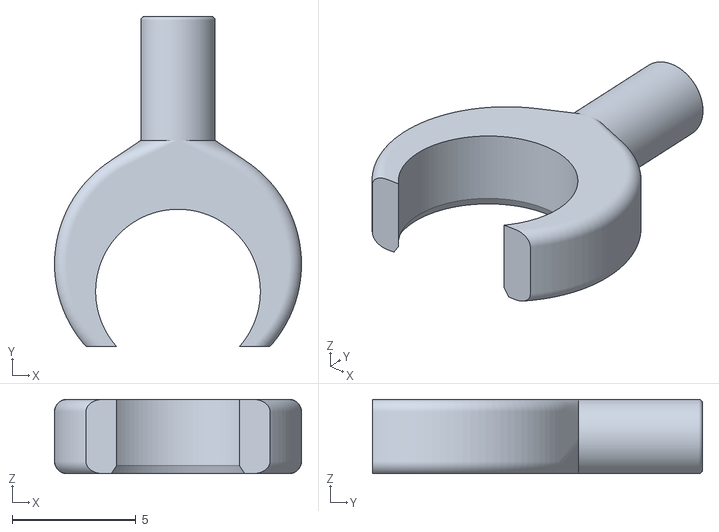
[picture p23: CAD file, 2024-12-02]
5_inch_pyramid_drone/3D_prints/canopy_snap_on_anchor.stl
9.97 x 13.3 x 3.00

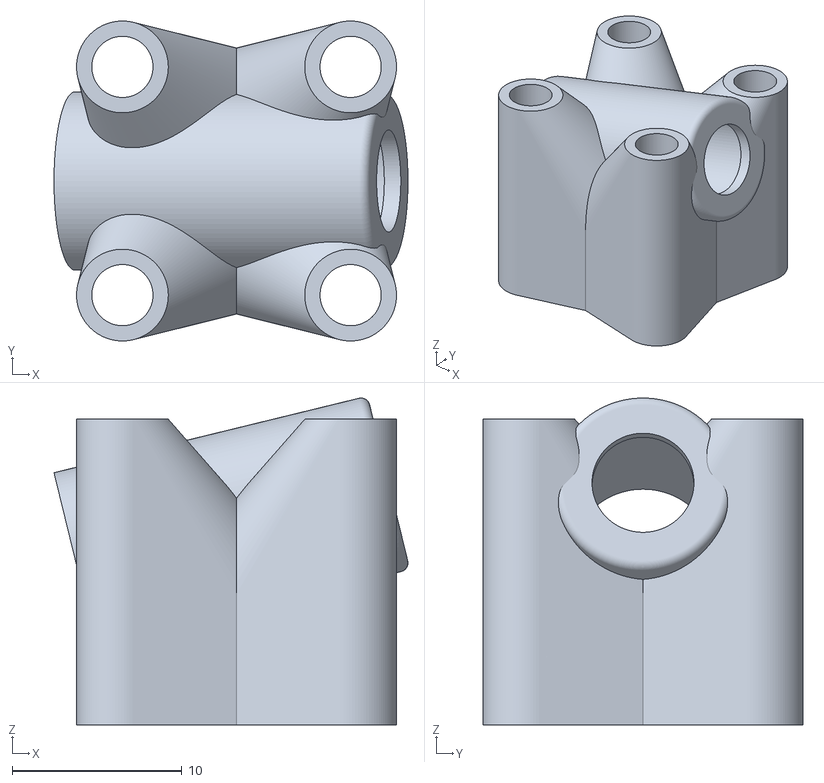
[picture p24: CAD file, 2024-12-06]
7_inch_pyramid_drone/3D_prints/hd_motor_mount.stl
20.8 x 18.8 x 19.2

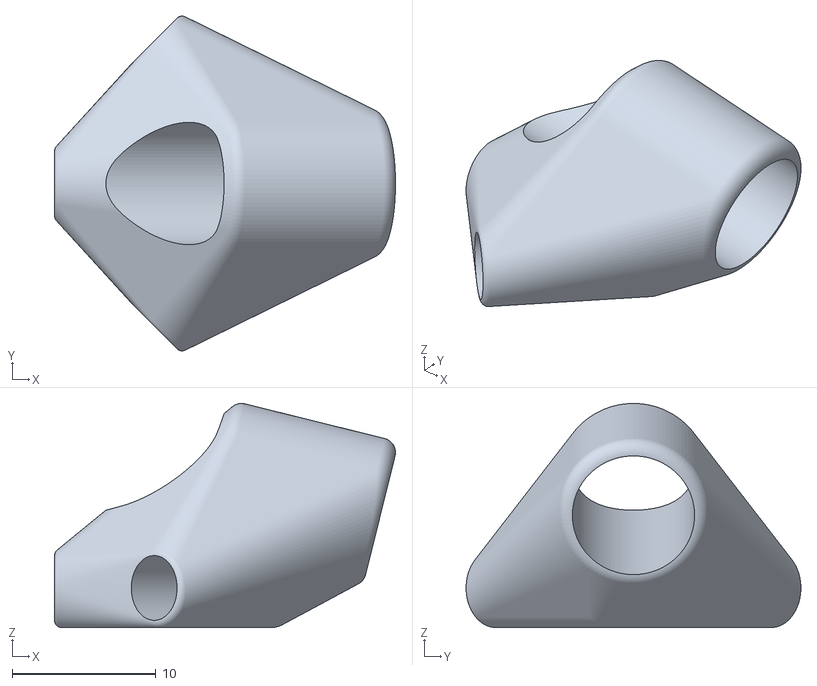
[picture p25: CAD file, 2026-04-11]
5_inch_hd_pyramid_drone/3D_prints/arm_corner_0.stl
23.7 x 23.3 x 15.6

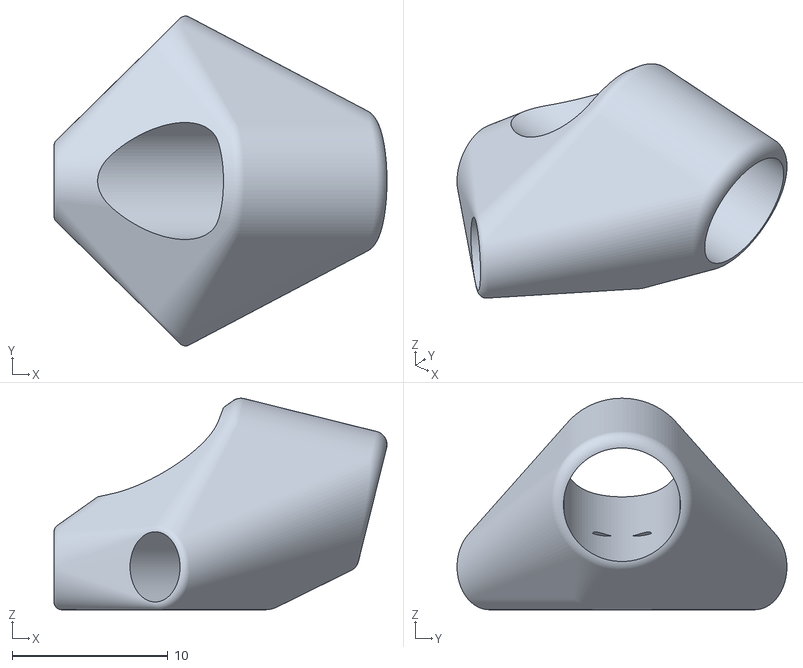
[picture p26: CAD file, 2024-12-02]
5_inch_pyramid_drone/3D_prints/arm_corner_node_0.stl
21.4 x 21.2 x 13.6

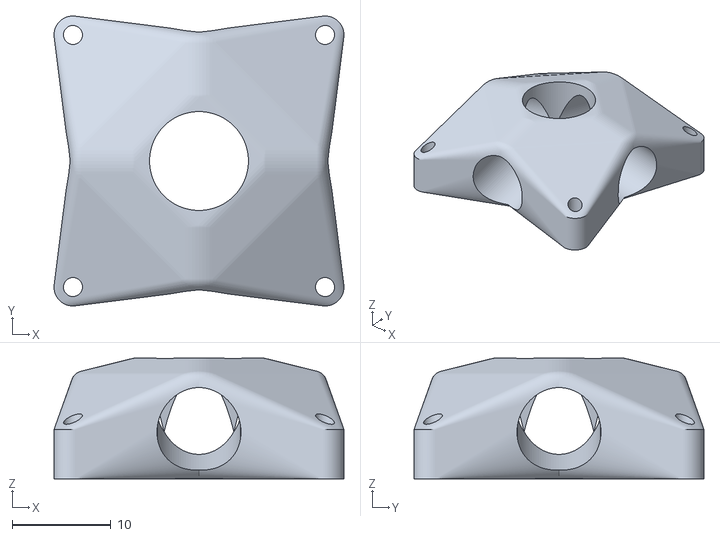
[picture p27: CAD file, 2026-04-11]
5_inch_hd_pyramid_drone/3D_prints/central_top_node.stl
29.3 x 29.3 x 12.2

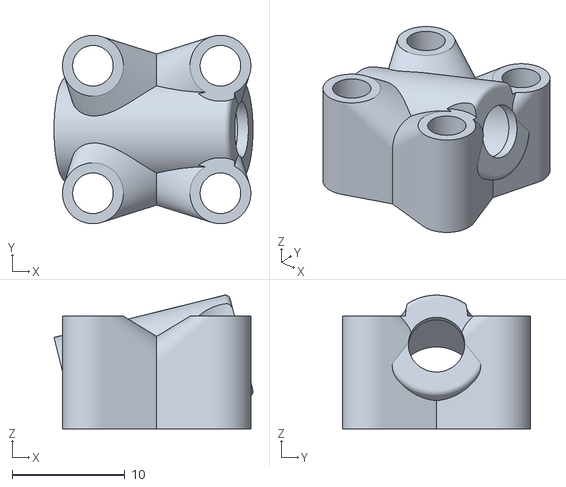
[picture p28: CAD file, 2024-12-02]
5_inch_pyramid_drone/3D_prints/motor_mount.stl
17.7 x 16.7 x 11.9

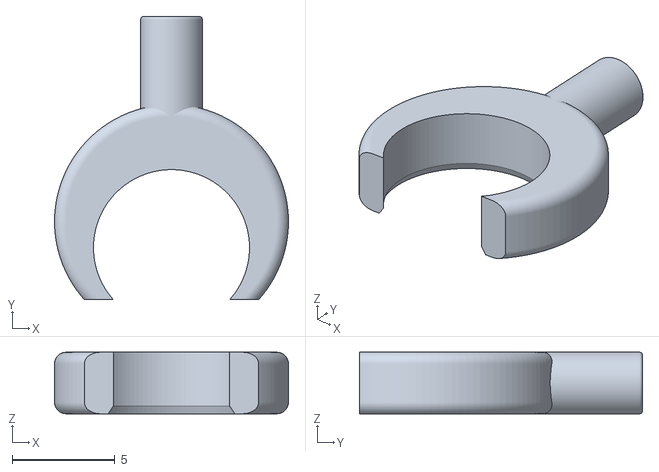
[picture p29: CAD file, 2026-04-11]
5_inch_hd_pyramid_drone/3D_prints/canopy_snap_on_anchor.stl
11.4 x 13.8 x 3.00

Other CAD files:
5_inch_pyramid_drone/3D_prints/arm_corner_node_1.stl
5_inch_pyramid_drone/3D_prints/canopy.stl
7_inch_pyramid_drone/3D_prints/canopy_long_camera_bolts.stl
5_inch_pyramid_drone/3D_prints/canopy_long_camera_bolts.stl
7_inch_pyramid_drone/3D_prints/arm_corner_0.stl
7_inch_pyramid_drone/3D_prints/arm_corner_1.stl
7_inch_pyramid_drone/3D_prints/battery_rail.stl
7_inch_pyramid_drone/3D_prints/canopy.stl
7_inch_pyramid_drone/3D_prints/canopy_snap_on_anchor.stl
7_inch_pyramid_drone/3D_prints/central_top_node.stl
7_inch_pyramid_drone/3D_prints/motor_mount.stl

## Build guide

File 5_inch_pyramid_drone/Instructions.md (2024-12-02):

# Build guide

## List of parts

### 3D Printed parts
* 1x `canopy.stl` (or `canopy_long_camera_bolts.stl`)
* 1x `central_top_node.stl`
* 2x `arm_corner_0.stl`
* 2x `arm_corner_1.stl`
* 4x `motor_mount.stl`
* 4x `canopy_snap_on_anchor.stl`
* (Optional) 4x `battery_pad.stl`

### Carbon tubing
* 1x 87.1mm long 4x2 tube (diagonal brace)
* 4x 64.5mm long 4x2 tube (perimeter brace)
* 4x 121mm long 7x5 tube (arm tube)

### Metal fasteners
* 16x M3x12mm motor bolts
* 4x M2x12mm flight controller mount bolts

### Tools and consumabled
* Structural epoxy, 30min set-time is ideal, or alternatively MMA adhesive
* Small cut-off saw for cutting carbon tubing (hacksaw with very fine toothed blade works as well)
* Small strip of sandpaper of flat file to scratch tube mating surfaces

### Drone parts
* 1x AIO board (Speedybee F405 AIO is a good choice)
* 4x 16mm mount pattern motors, 2207 size is a good choice
* 4x 5-6" Props (6" is the max diameter supported by the frame)
* Small size race type VTX (DarwinFPV Ape 25-600mW is a good choice)
* Short (40mm) u.FL antenna
* Micro sized cam (19mm camera spacing)
* RX (Small size like HGLRC ELRS 2.4G like is a good choice)

## Assembly instructions

### Assembling the frame

Print all parts with suitable material, ASA, PCTG or PA12CF15 are all good choices.
PLA/PETG are too brittle and their impact resistance is poor, so it's better to avoid them.

Standard print settings with 2-3walls, 20% infill and 4 top/bottom layers are good, keep cooling
at minimum (max 40%) to achieve good layer adhesion, no supports are necessary.

Cut CFRP tubing to necessary length using cut-off saw with carbide/diamond cutting disc (fastest and cleanest method),
or manual hacksaw with fine toothed blade. 
Try to cut the tubes as precisely as possible, it's better to cut the tubes little bit longer and carefully shorten
them to desired length with flat diamond file.

Once tubes are cut, you need to throughly scratch the mating surfaces with flat file for a good epoxy bond.
Scratching is not necessary with raw carbon pultruded tubes, like [DPP pultruded tubes](https://www.dpp-pultrusion.com/en-NL),
it's enough to clean and degrease them with IPA.

Next step is glueing the frame together. I recommend good structural epoxy with 30min set-time - while MMA adhesives
like [MD Megabond 3000](https://www.marstondomsel.de/index.php/en/product/md-megabond-3030) provide the best strength and
impact resistance, their set-time is usually quite short and their fumes are nasty.

It's easiest to divide glueing into 3 steps:
1. First, glue motor mounts on arm tube ends - test with a dry fit before, motor mount need to fit onn tube without excessive force.
Mix epoxy and apply it to the scratched/sanded end of the motor arm tube, then insert the tube into motor mount.
Make sure the tube is inserted all the way and rotate it couple of times to distribute epoxy evenly.
Be carefull to not clog the end of the tube with epoxy as it needs to be free for motor cable routing - remove the excess epoxy with piece of paper/towel in case some got into the tube.

2. As a second step, assemble the central support perimeter with diagonal tube.
Do a dry fit test before, making sure that tubes can be inserted into corner nodes easily and perimeter is square and lying flat on workbench.
Next, mix epoxy and put it inside each support tube hole/cavity (use a wooden stick for that).
Take 2 bigger corner nodes, mount them on diagonal tube and lay it on the workbench.
Take one of the smaller corner pieces and put 2 perimeter tubes into holes/sockets, repeat the same process for the last corner piece.
In the final assembly step, pull the 2 bigger corners with diagonal tube little bit apart and join it with rest of the pieces.
Once every tube is inside corner piece socket, press all corners together with your fingers and lay it flat on workbench.
You will need to wait till the epoxy cures for the last step.

3. Next, prepare the arm tubes with already mounted motor mounts (step 1) - make sure the through holes for 12mm long motor bolts are clear and bolts
can be inserted without problems. 
Once all bolt channels are ready, mount the bolts into motor mount, fixing them with nuts on the other side, so they don't fall out.
Alternatively, you can already mount motors with all 4 bolts, make sure the motor wires are facing outside the frame center, exactly opposite how would you normally mount them on a classic quad frame.

Test fit by inserting arm tubes (already with attached motor mounts) through the corners and joining them together with the central top node.
The best way do do it, is to first put 2 arm tubes through the smaller corner nodes (the ones joined by just 2 perimeter tubes, without the diagonal tube), and join them with the central node.
You can then use the cable hole in the central node + diagonal tube below it to visually center the arm tubes - put the remaining 2 arm tubes through the bigger perimeter corners afterwards and join them in the central node as well.
They should fit easily without excessive force and you should be able to easily rotate the arm tubes when the whole frame is assembled.
Put the frame on flat workbench, arm ends with motor mounts should be level when they rest on motor bolt heads and frame shouldn't be twisted, all 4 arm ends should be touching the bench.

Next, pull the arm tubes little bit (1-2cm) apart and remove the central node.
Mix epoxy and spread it on the arm tube just outside of the perimeter corner, cover a ~10mm band on the tube with epoxy, don't put too much there, just a thin layer.
Lift the frame (hold it by the perimeter tubes, avoid touching epoxied or to-be epoxied parts) and slowly push the arm tube you just epoxied ~2cm inside through the corner piece while rotating it at the same time, then pull it back.
The aim is to evenly spread the epoxy inside the corner piece, repeat for the each arm-tube/corner.
As a last step, spread epoxy on arm-tube ends (to be joined by the central top node), be careful to just spread it on the outside of the tube. Attach the central node, using the same sequence of steps as described
above in the (dry) fit test section, rotate each arm tube 2-3 times to spread the epoxy evenly, make sure that each tube is inserted fully to the end-stop in the central node and put the frame on flat workbench.
Make sure everything is aligned and level and wait for the epoxy to fully cure.

### Assembling the canopy housing

Put a bit of glue (epoxy or CA) on protruding sticks of canopy anchors and insert them into canopy anchor sockets.
Rotate the anchors in correct fashion - you can snap the canopy on frame and the anchors will align, wait for glue to set befor removing the canopy.

### Mounting frame components

1, Start by mounting motors, bolt each motor to mount on arm end in such a way that wires face outside of the frame center. 
Do not shorten the motor wires, you need at least 15cm long wires when routed internally.
Guide the wires through the hollow arm tube till you can see the wire ends in central node hole, then "fish" them out from the top hole with a help tweezers or small piece of bent wire. 
Once you have all 3 motor wires out tie them together with a small strip of tape, so you don't mix-up wires from separate motors later, 
when soldering them to ESC pads. 
You can even color mark wire before routing them through the tube, so you can solder them in the right order and you don't have to mess-up with motor direction in firmware later.

Alternative annd bit easier way is to mount motors in a standard way, with wires facing inwards, simply taped to the tube top side.
I think it's a shame to not take advantage of the unique internal routing capability of this frame and resulting better aesthetics & aerodynamics, but it's up to you.

2. Prepare AIO board by soldering battery leads, capacitor and CAM/VTX/RX connections.

3. Mount AIO board by placing it between top node and diagonal bracing tube and screwing bolts (M2x12mm) directly to holes in the central node.
Board needs to be flipped upside down, so that USB connector and solder pads are accessible.

After board is fixed, solder the the motor wires to ESC pads.

4. Fix the camera inside canopy with side bolts, connect it to camera wire from AIO.
Guide the short VTX antenna with uFL connector through the antenna tube and connect it to VTX.
Fix VTX with piece of double sided tape on canopy roof, fix RX board with double sided table inside canopy as well,
good place is front below the camera window.
Now you can tuck-in all connector wires inside canopy and snap canopy in place.

5. Secure RX antenna with zip tie or electrical tape on one the front arms (7mm) or front perimeter tube (4mm) if you use antenna with short lead.
Secure battery leads from AIO on rear perimeter tube (4mm) with zip tie as well.

### Mounting battery

Battery is mounted below the frame and you have 2 options how to secure it.

1. First option is to print 4 battery pads, put strips of non slippery silicone tape on them and snap them on front/back perimeter tubes (4mm).
Adjust their position according to battery width (they have raised edges to better secure battery against side to side movement)
and secure the battery with standard battery strip running below both side perimeter tubes + diagonal tube.

2. Alternatively, you can just fix the non-slipper silicone tape directly on battery side and mount the battery without additional pads,
battery will be resting directly against front/back and diagonal tubes.

### Betaflight configuration

Make sure to correctly adjust board/gyro position as flipped because you mounted the board upside-down, make sure to verify
it's behaving correctly.
Also make sure to correctly assign motors and their direction in the motors tab, especially when you didn't mark the motor wires
when routing them internally through arm tubes.

The quad flies very well on standard betaflight settings, even better with RPM filtering enabled and 5" Supafly preset.

[Flight video with 5" Supafly preset](https://www.youtube.com/watch?v=JDnkSyWG7Kg)

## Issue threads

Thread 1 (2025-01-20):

Durability

Quick-Flash, 2025-01-20:
Have you done any crash testing? I understand that it is more stiff than most 5 inch frames, but if any part breaks it'll require a complete rebuild. Have you considered using rolled carbon tubes instead of the pulltruded tubes?
This is a very interesting design, I'm just wondering how feasible it is to make one using carbon fiber nylon filament as in other testing I have done that is far, far more durable than PLA or PETG, but I do worry about how well it will glue.
I'm particularly worried about the motor mounts, I'd imagine its not too hard to get into a crash where the motors want to twist along the arm and end up causing the glue bond to break, or just break the print.

janherich, 2025-01-20:
@Quick-Flash

Regarding tubes, the they are fairly thick-walled and even in pultruded versions, they have good crush resistance, for bigger dimensions like 8mm OD main arm tubes, I'm using [pull-winded tubes](https://rotorbuilds.com/pictures/f_75660_sUtjg3rWJpcm48rFCupbQdOeu.jpg).

I had a fair amount of crashes, and I updated the design multiple times, taking the lessons into account, resulting in changes like:

* Motor mount using long bolts going through the whole part which are hugging the arm tube + compressing the motor across the Z direction (layers). Previously, the motor mounts used regular short bolts + bolt channels, that was not very durable because the tall motor mount "tower"  was loaded in bending in the worst possible direction and sometimes the motor mount snapped in relatively benign prop-strikes.
In contrast, motor mounts are now super-durable and since that change, I never broke that part, even in serious crashes where the whole frame was destroyed.
Downside is slightly higher weight from longer bolts and necessity to use separately sourced longer bolts not coming with motors (12mm M3 for the 5", 20mm M3 for 7").

* Beefier central node, as that was the weakest point after fixing design of motor mounts, sometimes in harder landings, it cracked and because it's normally hidden, it was hard to notice -> but frame was suddenly a lot more flexy in torsion and flew like shit with a lot of vibrations, this was problematic especially in cold freezing weather

So now I'm quite happy with crash resistance, quads are able to survive light crashes, harder landings, etc. just fine.
Of course, they will never be as rugged as classic frames, and things like fall from treetop height, collision with hard object at speed etc. will always result in destroyed frame.

That said, repairing the frame after crash is actually super cheap -> tubes almost always survive without any problems, same with motor mounts, so it's just mater of printing new central node + 4 corner nodes, cleaning tubes and reassembling the frame.

Regarding materials, PA12-CF15 works very well and glueing is not a big problem. Epoxy has good adhesion to (scratched/sanded) CFRP and poor to most plastics, but here it works more on a principle of interference fit -> gap between cfrp and inside of 3D printed socket is filled with epoxy and because inner texture of 3D printed is quite rough, it provides very good mechanical (if not chemical) bond.

vaska1992, 2025-01-20:
So you're saying that basically carbon tubes never breaks in crash, its always the 3d printed parts?
With that, i'd say a strong enough filament needs to be found for it. I think nylon is perfect for it, it probable will never break, but its hard to print it.

Quick-Flash, 2025-01-20:
> So you're saying that basically carbon tubes never breaks in crash, its always the 3d printed parts?
> With that, i'd say a strong enough filament needs to be found for it. I think nylon is perfect for it, it probable will never break, but its hard to print it.

Carbon nylon is easy to print. I've made a few frames with it, that were quite durable, but it always ended up working poorly as the nylon would absorb water and get less stiff to the point that it didn't fly well. These look like they won't have that issue.

janherich, 2025-01-20:
@vaska1992 Yes, although that's expected and I would even say preferable. Nylon is fine, it's around the same strength as PLA/PETG, but less stiff with much higher elongation at break, so it would be able to absorb a lot more energy before breaking, theoretically improving the durability of the frame a lot.
There are couple of potential problems with that though:
* FDM printed nylon unfortunately doesn't exhibit as good elongation at break and toughness in Z direction compared to X/Y
* You would need to use matching epoxy/glue, which is also not brittle and stiff, but tough and elastic, otherwise glue bond would break/shatter
* Introducing elasticity to nodes would decrease the stiffness of frame (but maybe dampen/isolate vibrations from motors for example...)

It's an interesting idea and maybe frame with less stiff but much tougher nodes from nylon/hard tpu would work well enough.

@Quick-Flash I suggest you try PA12 nylon, it doesn't have moisture absorption problems associated with more common PA6/PA66 nylons

Quick-Flash, 2025-01-20:
> [@Quick-Flash](https://github.com/Quick-Flash) I suggest you try PA12 nylon, it doesn't have moisture absorption problems associated with more common PA6/PA66 nylons

I can't remember which nylon I used, it was one of polymakers, I can check later though. From this graph pa612 will give the best results. PET CF17 also looks interesting and fairly cheap https://us.polymaker.com/products/fiberon-pet-cf17?variant=44225304231993
However wet PA6 CF20 has very good impact strength when wet (supposedly 3 times greater than PETG). So if it is stiff enough while wet, then it would make for a pretty durable frame.

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

Quick-Flash, 2025-01-20:
I've also been thinking of the possibility of using some sort of screw mechanisms to hold the frame parts together.

Maybe something like hose clamps to hold parts together? If not those there has to be something that could clamp the tubes well enough to not require glue, but maybe I'm overly optimistic.

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

Quick-Flash, 2025-01-20:
I've thought of having two cross braces under the flight stack instead of just 1. You'd need to file down some CF tubes and glue them together to make it work.
Kind of like this guide. https://imgur.com/a/building-tube-frame-hEevI

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

janherich, 2025-01-20:
@Quick-Flash good ideas with tube clamps, the tool I'm using to generate spaceframe nodes support many node types, including screw-types, I used them extensively for my [3D printers](https://www.spacedelta3d.com/printers.html), where links are stainless steel tubes -> but it will always be a lot heavier for the same stiffness and more bulky/less aerodynamic compared to sleek joints with just epoxy bonds.

Regarding the diagonal tube, as it's solid tube which is very similar stiffness in both compression and tension, it's unnecessary to add a second diagonal tube, the base is fully triangulated as it is -> if it was wire brace which works only under tension, then yes, cross-bracing would be necessary (and it would save some weight, but require proper tensioning).
Not worth for small 5/7/10" quads, but could be very interesting for truly big quads -> it could actually work with no glue/adhesive at all, using wires with loops at the ends, notches in corners to secure the loops and dry sockets in corners for perimeter tubes (wire tension would push the 4 perimeter tubes into sockets), only central node would need tube clamps... Thanks for the idea !

Quick-Flash, 2025-01-20:
@janherich you mentioned that the central mount where the FC goes was a weak point. What if there was a small piece of flat carbon (0.5-1mm) that you glued to the top and bottom of it, then when you put your FC on you can clamp the two carbon pieces in between the printed parts and get a piece that is much stronger in the Z direction.

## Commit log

2024-12-02 5 inch drone
    [arm_corner_node_0.stl, arm_corner_node_1.stl, battery_pad.stl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]
2024-12-03 Tweak central top node
    [central_top_node.stl]
2024-12-03 Modify readme to better explaing material choices
2024-12-03 Tweak readme and add 7inch files
    [arm_corner_0.stl, arm_corner_1.stl, canopy.stl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]
2024-12-03 Add 7 inch files and readme
    [battery_pad.stl]
2024-12-04 Add battery rails for 7inch drone + info in readme
    [battery_rail.stl]
2024-12-06 HD motor mounts + fixed battery rail dimensions
    [battery_rail.stl, canopy.stl, canopy_long_camera_bolts.stl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]
2024-12-06 Tweak rail length
    [battery_rail.stl]
2024-12-06 Dimensions tweak
    [battery_rail.stl]
2024-12-20 Material update + revised battery mount info
    [battery_pad.stl, battery_rail.stl]
2024-12-31 Beefier central nodes
    [central_top_node.stl]
2026-01-29 Copy changes
    [battery_rail.stl]
2026-04-11 Add HD version
    [arm_corner_0.stl, arm_corner_1.stl, battery_rail.stl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]
2026-04-12 Add sample build sections
